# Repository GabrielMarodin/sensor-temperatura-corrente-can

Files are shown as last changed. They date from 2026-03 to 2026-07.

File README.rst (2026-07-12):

Monitoramento de temperatura e corrente via CAN do barco solar
#####################################################################

.. contents::
   :local:
   :depth: 2

Requisitos
**********

Este projeto foi implementado com os seguintes módulos/softwares/hardwares:
 | Sensor de temperatura PT100 com 3 fios.    
 | Sensor de corrente de efeito Hall LEM LA 205-S.  
 | MCP2515 (Controlador CAN);
 | TJA1050 (Transceptor CAN);  
 | Linguagem de programação C.  
 | Microcontrolador STM32F401 com SPI, ADC e regulador de 5V para 3V3.  

Visão geral
***********

Esse projeto faz parta do barco solar Zênite Solar.

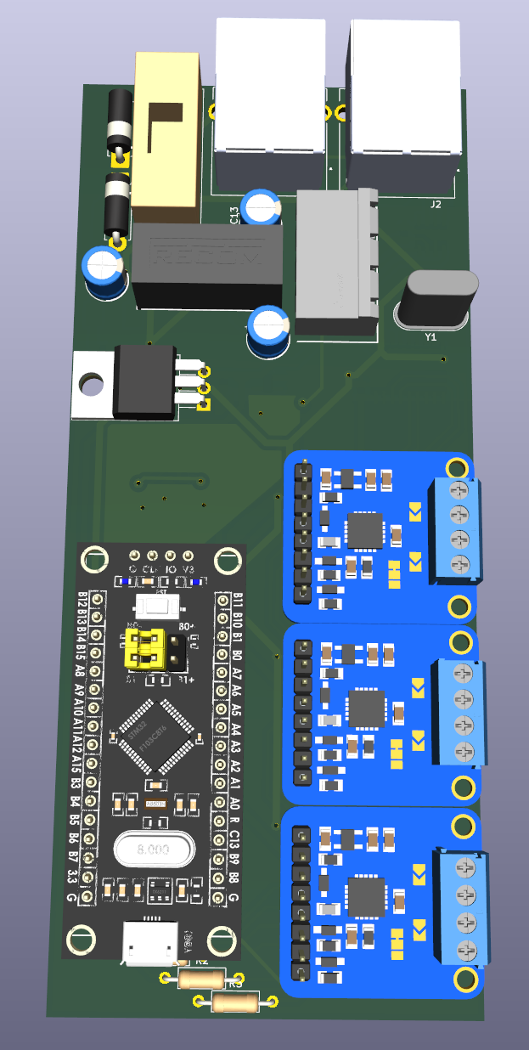
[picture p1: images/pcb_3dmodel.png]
Modelo 3D da placa de circuito impresso


É um sistema microcontrolado embarcado ao barco que possui capacidade de ler temperaturas em pontos estratégicos do barco e a corrente do motor.

O microcontrolador lê e trata os dados e empacota em um frame CAN para transmitir, através a implementação do controlador e transmissor CAN, para a saída do conector RJ45.

O desenvolvimento foi divido em quatro etapas:

- `Etapa 1 </etapa_1>`_ (02/04/2026): Pesquisa, planejamento e outline do projeto.
- `Etapa 2 </etapa_2>`_ (30/04/2026): Teste dos módulos e desenvolvimento de protótipo.
- `Etapa 3 </etapa_3>`_ (28/05/2026): Desenvolvimento do produto.
- `Etapa 4 </etapa_4>`_ (09/07/2026): Implementação e análise de desempenho.

Interface do usuário
********************
LED de respiração:
  Pisca enquanto o RTOS estiver ativo.

Testando
========

Para testar pode ser usado o debugger do microcontrolador para ler as variáveis e registradores ou um analizador de CAN para capturar as mensagens transmitidas.

Montagem
********

O sistema é alimentado e transmite os frames CAN pelo conector RJ45;

O sensor de corretente de efeito hall deve ser conectado no conector de 4 pinos;

O PT100 deve ser conectado no MAX31865 nos conectores de parafuso.

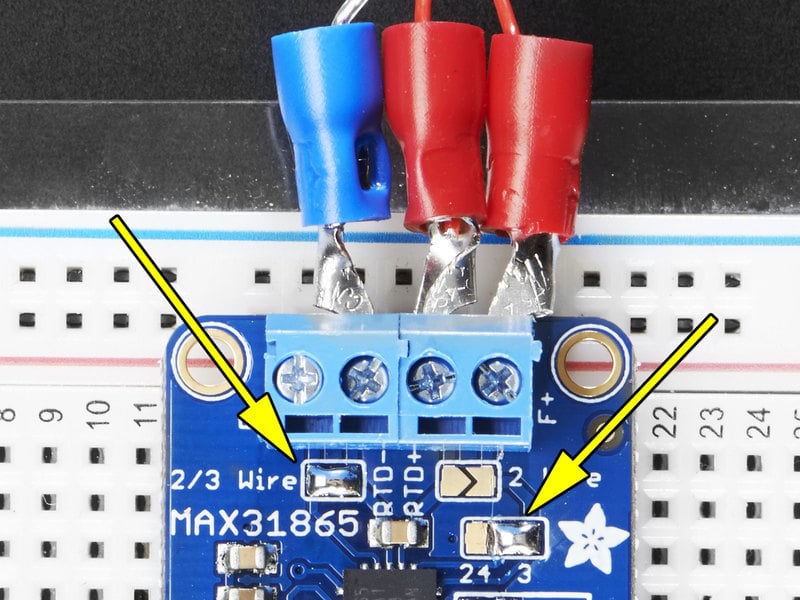
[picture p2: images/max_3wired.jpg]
MAX31865 breakout board com 3 fios conectados


   Modo de conexão de 3 fios do PT100.

   No modo 3 wires 2 fios estão em paralelo e 1 fio tem 100 ohms de resistência a 0 graus celsius em relação aos outros, os fios com resistência muito baixa entre si devem ser conectados em RTD+ e F+, enquanto o terceiro fio deve ser conectado em RTD-.

Referências (Links)
*******************

- `GitHub do Zênite Solar <https://github.com/ZeniteSolar>`_

- `Firmware do Projeto </etapa_4/Firmware>`_

- `Projeto KiCad da PCB </etapa_3/PCB/Modulo_corrente_temperatura_barco_Zenite>`_

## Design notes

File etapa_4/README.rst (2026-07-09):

Etapa 4
#######

.. contents::
   :local:
   :depth: 2

Visão geral
***********

A Etapa 4 abordará projeto do layout e montagem da placa de circuito impresso que abriga o sistema embarcado. A partir da montagem da PCB serão verificados os critérios de desempenho definidos na Etapa 3, juntamente a validação do sistema e integridade dos dados no barco.

Desenvolvimento
***************

Layout da PCB
=============

Para a elaboração do *layout* foram priorizados os seguintes aspectos:

+ Alta densidade de componentes, visando aproveitar o espaço limitado;
+ Segmentação da placa em áreas relacionadas à potência (dissipação de calor e emissão de EMI), tratamento de sinais analógicos e trilhas de sinais digitais;
+ Dedicação de um plano de referência exclusivo para o condicionamento do sinal proveniente do sensor de corrente (visando diminuir erros e aumentar a precisão);
+ Priorização de componentes SMD;
+ As regras de desenho devem ser compatíveis com os limites da CNC do LPAE(IFSC);
+ Placa de face dupla, sendo a camada superior majoritariamente um plano de referência sólido.

Observando as condições de manufatura do IFSC, foram priorizados componentes SMD de tamanho mínimo equivalente ao encapsulamento SOIC para os circuitos integrados e 0805 para capacitores e resistores. O projeto desenvolvido no KiCad pode ser visualizado em: `Link para a versão 1 do projeto <https://github.com/GabrielMarodin/sensor-temperatura-corrente-can/tree/main/etapa_3/PCB/Modulo_corrente_temperatura_barco_Zenite>`_ .

No entanto, alguns componentes estavam indisponíveis e adaptações foram necessárias, como pode ser observado na imagem abaixo.

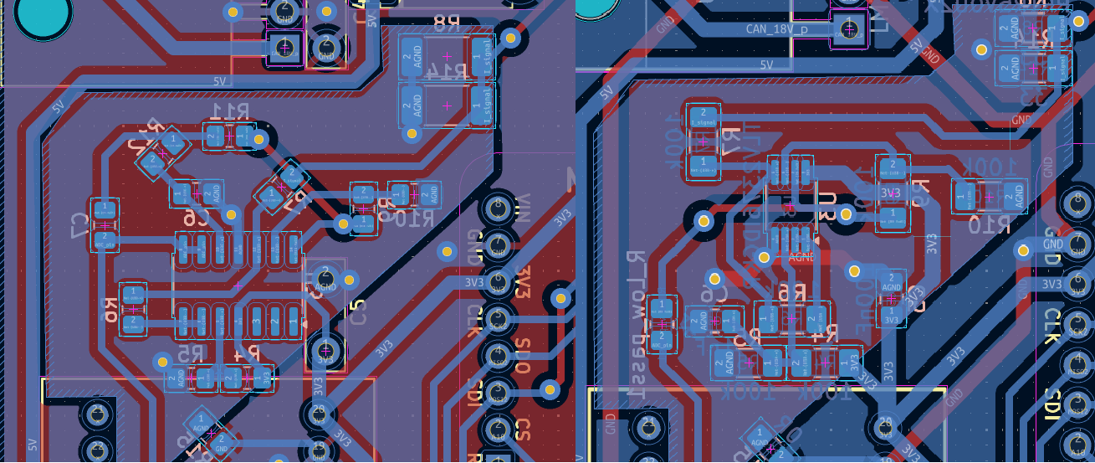
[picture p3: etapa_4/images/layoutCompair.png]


O amplificador operacional TLV9004, inicialmente idealizado, foi substituído pelo TLV2376, em um encapsulamento menor, mas plenamente compatível com os requisitos do projeto. A substituição também ocorreu com o filtro ativo anteriormente previsto que foi trocado por um filtro passivo RC passa-baixa. O *layout* adaptado no KiCad pode ser visualizado em: `Link para a versão 2 do projeto <https://github.com/GabrielMarodin/sensor-temperatura-corrente-can/tree/main/etapa_3/PCB/Modulo_corrente_temperatura_barco_Zenite-V02>`_ .

Montagem da PCB
===============

A fabricação da PCB foi realizada no LPAE com o auxílio de seus técnicos e professores para a operação da CNC. O projeto impresso corresponde à `versão 2 <https://github.com/GabrielMarodin/sensor-temperatura-corrente-can/tree/main/etapa_3/PCB/Modulo_corrente_temperatura_barco_Zenite-V02>`_ . No entanto, algumas modificações foram necessárias, como o corte manual das trilhas e pads do amplificador operacional, além da utilização da técnica de *wire up* para integrar o circuito integrado à placa.

A PCB montada pode ser visualizada nas imagens abaixo:

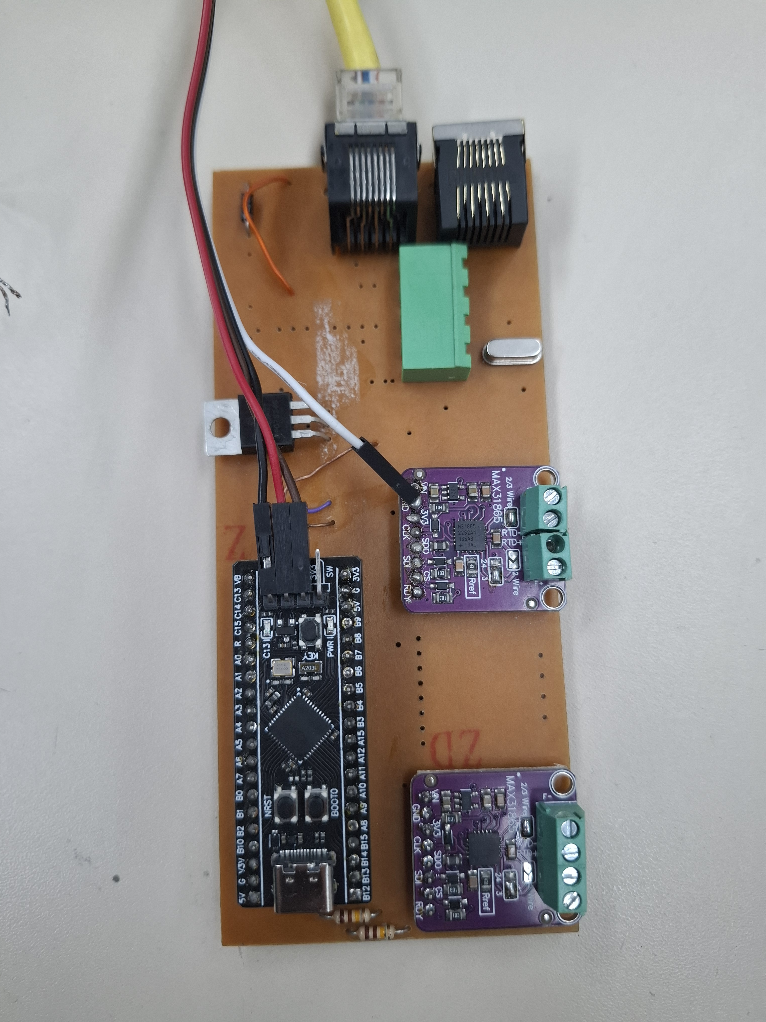
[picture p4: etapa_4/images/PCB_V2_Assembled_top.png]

   
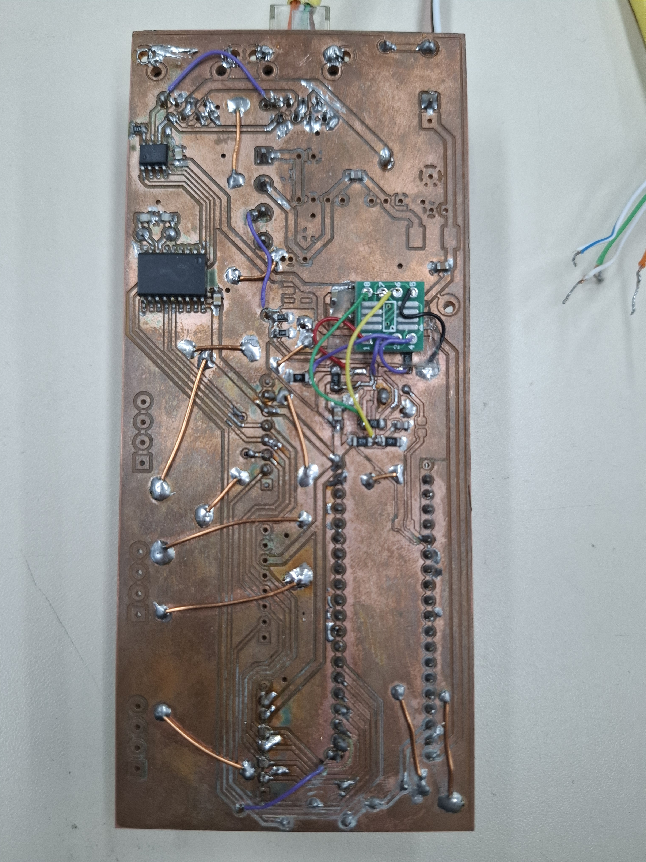
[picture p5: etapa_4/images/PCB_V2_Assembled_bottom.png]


Nota-se nas imagens que há muitos espaços não ocupados por componentes. Esses espaços correspondem a elementos que não estavam disponíveis no momento da montagem, mas que poderão ser inseridos posteriormente, assim que houver disponibilidade. Observa-se também a presença de diversos fios de cobre nu esmaltado na parte inferior da placa. Esses fios foram utilizados para interconectar as ilhas de GND, uma vez que não foi possível fabricar a placa em dupla face e garantir o plano de referência sólido originalmente previsto.

Validação da Aplicação
======================

Validação do Desempenho
***********************

Sensor Hall
======================

O sensor de efeito Hall lido pelo ADC com offset teve os seguintes resultados:

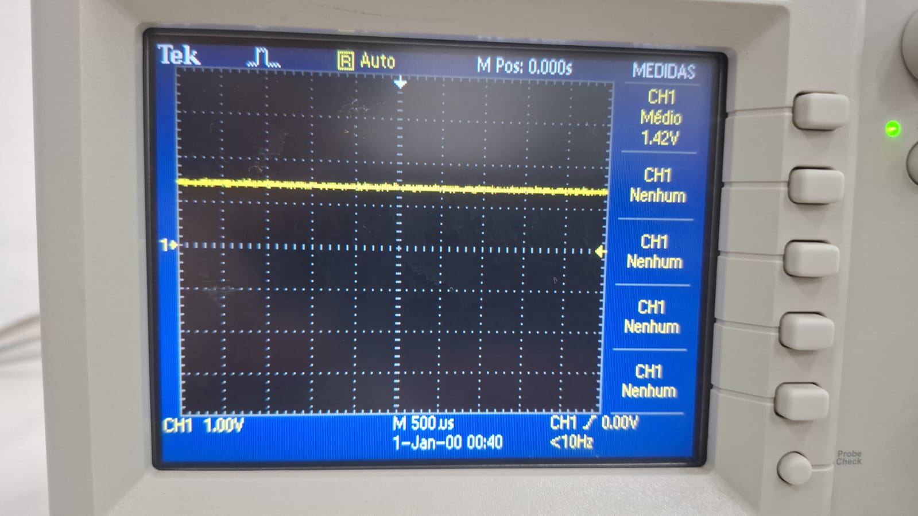
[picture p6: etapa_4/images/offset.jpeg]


A figura mostra o valor real medido do offset no divisor resistivo.

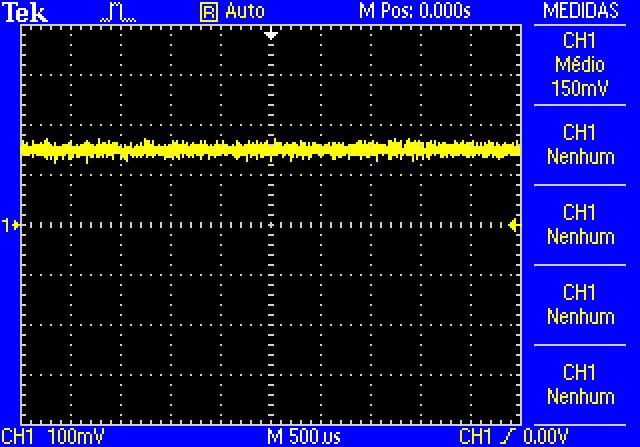
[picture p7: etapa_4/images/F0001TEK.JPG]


A figura mostra o valor de tensão com corrente positiva no shunt de 16 Ohms do sensor de corrente.

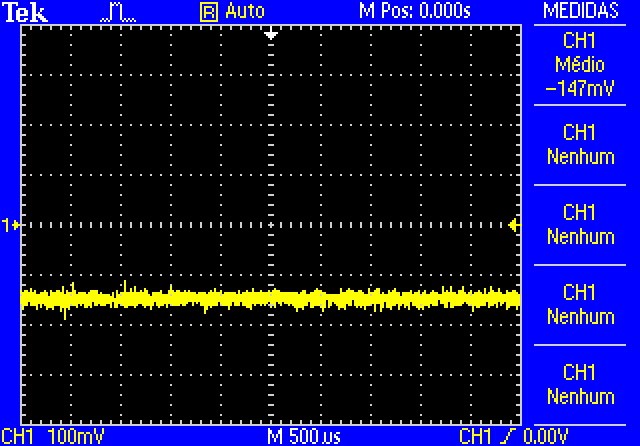
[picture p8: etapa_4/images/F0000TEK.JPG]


A figura mostra o valor de tensão com corrente negativa no shunt de 16 Ohms do sensor de corrente.



A figura mostra o valor lido e convertido utilizando a fórmula `previamente exposta na etapa 2 <../etapa_2/README.rst#L55>`_.

Pode-se concluir que há uma variação de 3 mA o que era esperado para a resolução de 10 bits mais as não idealidades propagadas.

Sensor de temperatura
======================

O sensor temperatura lido pelo SPI da breakout board MAX31865 teve os seguintes resultados:

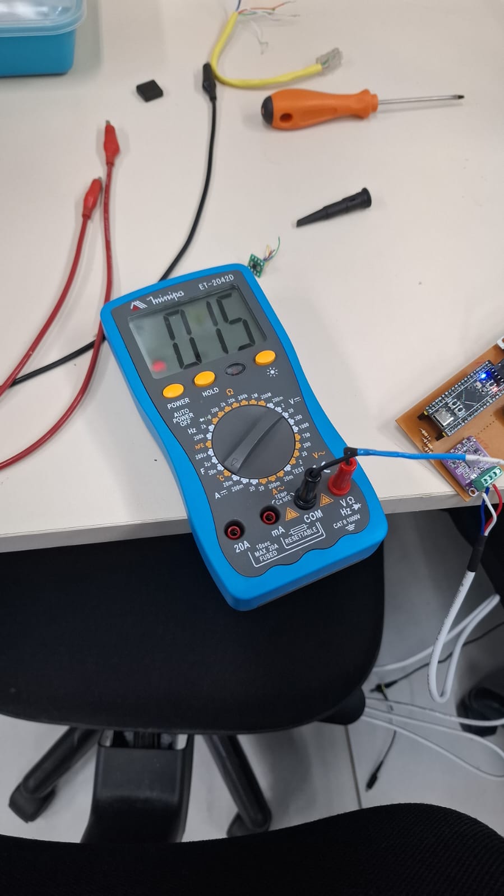
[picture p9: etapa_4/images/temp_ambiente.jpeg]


A figura mostra a temperatura ambiente no momento de teste.

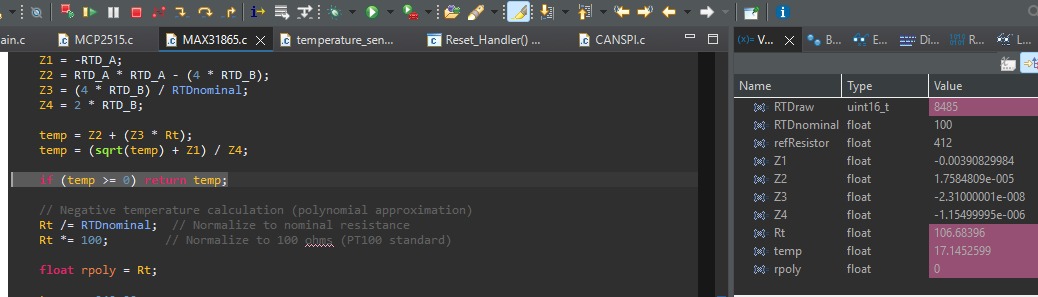
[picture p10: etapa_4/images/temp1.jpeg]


A figura mostra a temperatura lida e calculada do PT100.

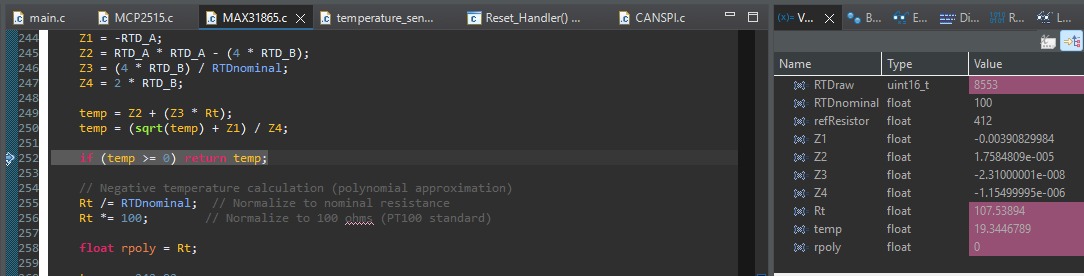
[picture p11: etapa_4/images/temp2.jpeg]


A figura mostra a temperatura do PT100 depois de um tempo em contato com a mão.

O ADC do MAX31865 é de 16 bits com 15 bits de RTD a resolução é alta e o maior fator de erro é o valor do resistor de referência, alterar a macro do software do [RREF] para o valor medido com um multímetro na hora 
afeta a exatidão da temperatura dastricamente.

Estimativas de processamento e desempenho do MCU
======================
Não houve tempo de executar testes quantitativos do processamento da CPU, portanto foram feitas estimativas baseadas
no tempo médio dos processos mais lentos de cada tarefa e gastos típicos de corrente e ocupação da CPU.

O período de ativação das tarefas é muito maior que o tempo de execução da tarefa mais lenta o que permite dizer que o sistema
não tem dificuldade em atender as deadlines e mesmo assim ele é soft real-time considerando que perdas de dados ocasionais não
causarão falhas críticas no sistema em que está embarcado.

Tempo de execução de cada tarefa
--------------------------------

+------------------+-----------------------------------------------+----------------------+
| Tarefa           | Descrição                                     | Tempo estimado       |
+==================+===============================================+======================+
| CurrentTask      | Processamento do buffer ADC                   | 20–60 µs             |
+------------------+-----------------------------------------------+----------------------+
| CANCurrentTask   | Cálculo RMS, pico e envio CAN                 | 180–350 µs           |
+------------------+-----------------------------------------------+----------------------+
| RTDTask          | Leitura de três sensores MAX31865             | 200–225 ms           |
+------------------+-----------------------------------------------+----------------------+
| CANTempTask      | Empacotamento e envio CAN                     | 70–120 µs            |
+------------------+-----------------------------------------------+----------------------+

Tempo de ocupação da CPU
--------------------------------

+---------------------------+----------------+
| Componente                | Utilização     |
+===========================+================+
| Processamento ADC         | 1–3 %          |
+---------------------------+----------------+
| Cálculo da corrente RMS   | 2–5 %          |
+---------------------------+----------------+
| Driver CAN                | < 1 %          |
+---------------------------+----------------+
| Escalonador FreeRTOS      | < 1 %          |
+---------------------------+----------------+
| Processamento RTD         | < 1 %          |
+---------------------------+----------------+
| Total estimado            | 5–10 %         |
+---------------------------+----------------+
| CPU ociosa                | 90–95 %        |
+---------------------------+----------------+

Medição do WCET (Worst-Case Execution Time)
--------------------------------

+------------------+----------------------+------------------------------+
| Tarefa           | WCET estimado        | Observação                   |
+==================+======================+==============================+
| CurrentTask      | 60 µs                | Filtragem e cópia DMA        |
+------------------+----------------------+------------------------------+
| CANCurrentTask   | 350 µs               | Inclui cálculo RMS e CAN     |
+------------------+----------------------+------------------------------+
| RTDTask          | 225 ms               | Inclui atrasos HAL_Delay()   |
+------------------+----------------------+------------------------------+
| CANTempTask      | 120 µs               | Montagem e transmissão CAN   |
+------------------+----------------------+------------------------------+
| RTDTask (CPU)    | 300–500 µs           | Desconsiderando HAL_Delay()  |
+------------------+----------------------+------------------------------+

Eficiência energética da placa
--------------------------------

+--------------------------------+-----------------------------+
| Parâmetro                      | Valor estimado              |
+================================+=============================+
| Frequência do processador      | 84 MHz                      |
+--------------------------------+-----------------------------+
| Consumo típico do STM32F4      | 25–35 mA @ 3,3 V            |
+--------------------------------+-----------------------------+
| Potência estimada do MCU       | 80–115 mW                   |
+--------------------------------+-----------------------------+
| Utilização média da CPU        | 5–10 %                      |
+--------------------------------+-----------------------------+
| Tempo ocioso da CPU            | 90–95 %                     |
+--------------------------------+-----------------------------+
| Uso de DMA                     | Sim                         |
+--------------------------------+-----------------------------+
| Uso de filas do FreeRTOS       | Sim                         |
+--------------------------------+-----------------------------+
| Polling contínuo               | Não                         |
+--------------------------------+-----------------------------+
| Classificação da eficiência    | Alta                        |
+--------------------------------+-----------------------------+

Verificação da Integridade dos Dados
====================================

Referências (links/datasheets/livros)
*************************************

- `Código de interface MCP2515 <https://github.com/eziya/STM32_SPI_MCP2515/tree/master>`_

- `Datasheet do MCP2515 <https://www.microchip.com/en-us/product/mcp2515>`_

- `Datasheet do MAX31865 <https://www.analog.com/media/en/technical-documentation/data-sheets/max31865.pdf>`_

- `Datasheet do TLV2376 <https://www.ti.com/product/TLV2376/part-details/TLV2376IDGKR>`_

- `Datasheet do TJA1050 <https://www.nxp.com/docs/en/data-sheet/TJA1050.pdf>`_

- `Fundamentos da camada física do CAN <https://www.ti.com/lit/an/slla270/slla270.pdf?ts=1783507668427>`_

- `GitHub do Zenite Solar <https://github.com/ZeniteSolar>`_

- `ARM Cortex-M4 Technical Reference Manual (DWT CYCCNT) <https://documentation-service.arm.com/static/5fce431be167456a35b36ade>`_

- `ARM Cortex-M4 Processor Datasheet <https://developer.arm.com/-/media/Arm%20Developer%20Community/PDF/Processor%20Datasheets/Arm%20Cortex-M4%20Processor%20Datasheet.pdf>`_

- `STM32F4 Series Documentation (Reference Manuals and Datasheets) <https://www.st.com/en/microcontrollers-microprocessors/stm32f4-series/documentation.html>`_

- `STM32F407/417 Documentation (Reference Manual RM0090 and Datasheets) <https://www.st.com/en/microcontrollers-microprocessors/stm32f407-417/documentation.html>`_

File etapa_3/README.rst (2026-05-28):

Etapa 3
#######

.. contents::
   :local:
   :depth: 2

Visão geral
***********

A Etapa 3 abordará a implementação do protocolo CAN, bem como a integração e os testes dos dados provenientes dos sensores em um mesmo firmware baseado em arquitetura RTOS. O objetivo é validar o envio correto das informações pelo barramento CAN.

Além disso, será abordado a elaboração do esquemático da placa de circuito impresso, juntamente com a definição dos critérios de desempenho do sistema, que serão avaliados na etapa seguinte.

Desenvolvimento
***************

`Link para os Testes <Testes>`_

Implementação do Protocolo CAN
==============================

O `driver </etapa_3/Testes/pi3_CAN_test/Core/Src/MCP2515_driver.c>`_ do MCP2515 se baseia na implementação da Microchip e utiliza o mapa de registradores do  `datasheet <https://ww1.microchip.com/downloads/en/DeviceDoc/MCP2515-Stand-Alone-CAN-Controller-with-SPI-20001801J.pdf>`_ (tabelas 11-1 e 11-2).
O MCP2515 é configurado para ter sua divisão de clock de 8 MHz de forma a transmitir em 500 Kbps;

Integração dos dados dos sensores à aplicação
=============================================

Os dados dos sensores foram arranjados da seguinte maneira:

Temperatura:

+-------------------+----------------+
|        Dado       | Tamanho (Bits) |
+===================+================+
|    Temp. Motor    |       10       |
+-------------------+----------------+
| Temp. Controlador |       9        |
+-------------------+----------------+
|   Temp. Bateria   |       10       |
+-------------------+----------------+
|  Falha Detectada  |        3       |
+-------------------+----------------+

Foi alterado para possibilitar o relatório de erro individual de cada sensor.

Corrente:

+---------------------+----------------+
| Dado                | Tamanho (Bits) |
+=====================+================+
| Corrente de Pico    | 12             |
+---------------------+----------------+
| Sentido do Pico     | 1              |
+---------------------+----------------+
| Corrente RMS        | 12             |
+---------------------+----------------+
| Sentido da Corrente | 1              |
+---------------------+----------------+
| Mensagem de Erro    | 7              |
+---------------------+----------------+

Estes dados foram integrados em pacotes com o seguinte código:

`sensor de corrente </etapa_3/Firmware/Core/Inc/current_sensor.h>`_:

.. code-block:: C

	typedef struct __attribute__((packed)) {
      uint32_t Peak_Current : 11; // Corrente de Pico
      uint32_t Peak_Dir     : 1;  // Sentido da Corrente de Pico
      uint32_t Current_RMS  : 12; // Corrente RMS
      uint32_t Current_Dir  : 1;  // Direção Principal da Corrente
      uint32_t Error_msg    : 7;  // Mensagens de Erro
   } Current_pkg;

`sensores de temperatura </etapa_3/Firmware/Core/Inc/temperature_sensor.h>`_:

.. code-block:: C

   typedef struct __attribute__((packed)) {
      uint32_t Motor_Temp  : 10; // Temperatura do Motor
      uint32_t Charge_Temp : 9;  // Temperatura dos Controladores de Carga
      uint32_t Batt_Temp   : 10; // Temperatura da Bateria
      uint32_t Error_msg   : 3;  // Mensagens de Erro
   } Temp_pkg;

- `Link para o firmware </etapa_3/Firmware>`_

Teste da Rede CAN com Dados dos Sensores
========================================
Após implementação em código do `sensor de corrente </etapa_3/Testes/Sensor_RTOS/Core/Src/Current_Sensor.c>`_ 
e dos `sensores de temperatura </etapa_3/Testes/Sensor_RTOS/Core/Src/Temperature_Sensor.c>`_, foi implementada 
à partir do `driver do MCP2515 </etapa_3/Testes/Sensor_RTOS/Core/Src/MCP2515_Driver.c>`_ a transmição dos 
dados dos sensores utilizando o protocolo CAN nos IDS 0x10 e 0x11. O teste foi realizado utilizando um 
`ESP 32 </etapa_3/Testes/ESP32devkit/ESP32MCP2515>`_ como nó receptor, com o blackpill STM atuando como 
nó transmissor enviando mensagens.

Segue uma imagem do teste da rede CAN, o osciloscópio mede a tensão diferencial da linha no módulo utilizado.

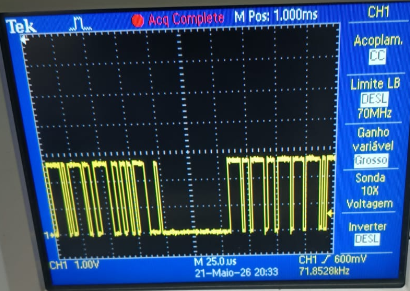
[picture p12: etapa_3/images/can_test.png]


O ESP32 foi configurado para repassar as mensagems que recebe por SPI do MCP2515 para a porta 
serial, e o terminal do computador foi configurado para receber as mensagens. Devido à um problema de comunicação,
não foi possível realizar a leitura da rede CAN.

Esquemático da PCI
==================

O projeto KiCad onde foi elaborado o esquemático pode ser encontrado em:  `Link para o Esquemático do Projeto <https://github.com/GabrielMarodin/sensor-temperatura-corrente-can/tree/main/etapa_3/PCB/Modulo_corrente_temperatura_barco_Zenite>`_ 

O esquemático apresentado em partes nos próximos tópicos foi desenvolvido para atender aos requisitos do projeto, considerando:

- Níveis de tensão e corrente necessários para cada sensor e circuito integrado.

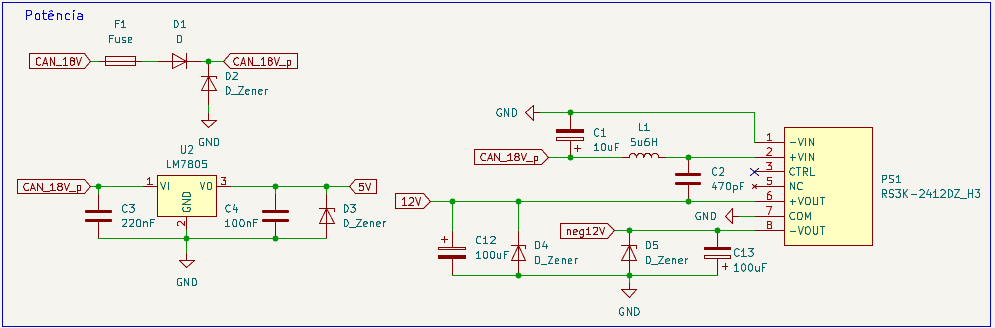
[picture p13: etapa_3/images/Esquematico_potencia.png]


Na figura acima é possível observar elementos de proteção contra sobrecorrente e surtos de tensão, além de um regulador linear destinado à alimentação do microcontrolador e de um conversor estático responsável por suprir as necessidades do sensor de corrente utilizado.

- Conexão com a rede CAN, alimentação do módulo e do sensor de corrente.

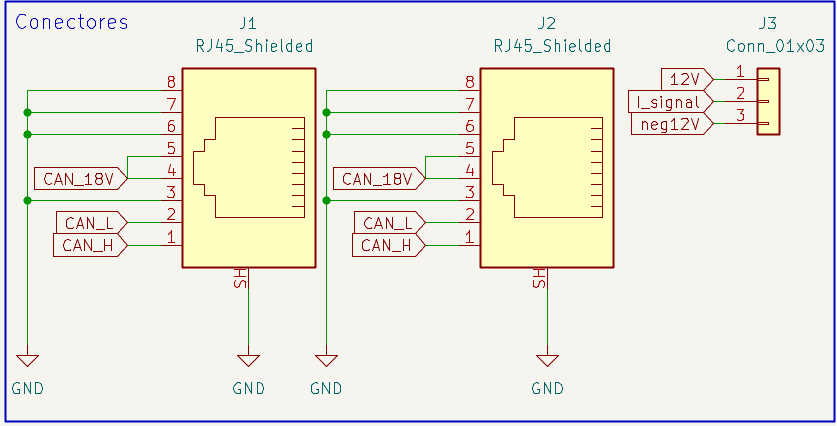
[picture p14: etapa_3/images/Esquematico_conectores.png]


Além dos conectores RJ45 padrão do barco foi necessário a previsão de um conector 3 pinos genérico para a alimentação e retorno do sinal em corrente do LA 205-s.

- Condicionamento do sinal de corrente do LA 205-s.

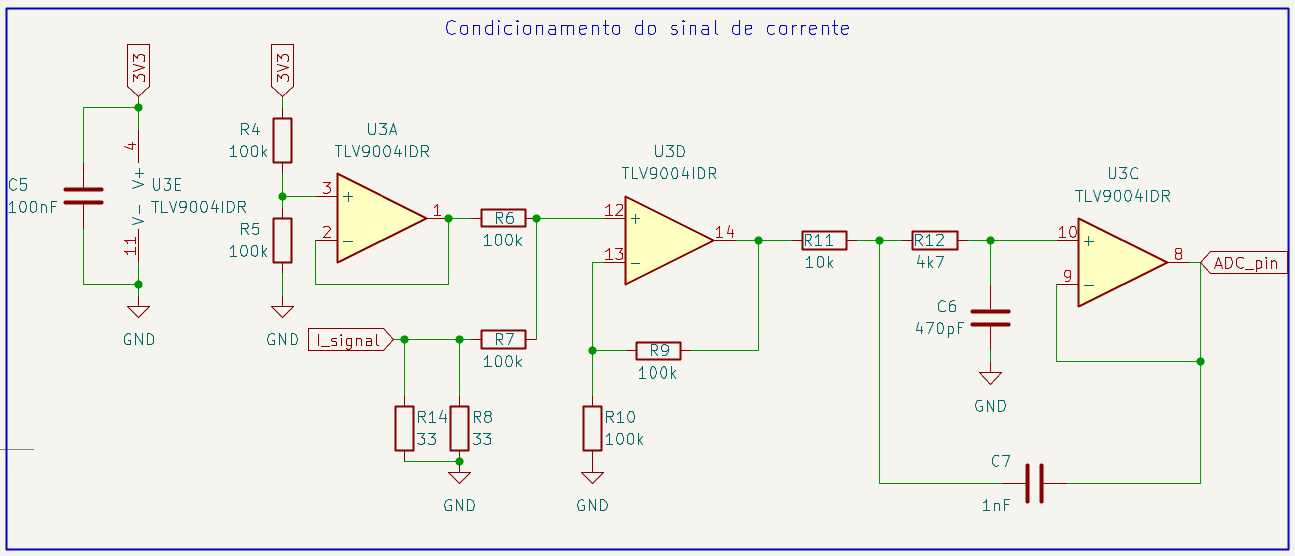
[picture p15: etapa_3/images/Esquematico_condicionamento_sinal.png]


Observa-se na figura a presença de amplificadores operacionais configurados em diferentes topologias: buffer (para sinal de referência), somador não inversor (para obtenção do offset) e filtro ativo passa-baixa de segunda ordem.

   O circuito funciona de modo que:

   - 1,65 V na saída representam 0 A;
   - 3,3 V na saída correspondem a +200 A;
   - 0 V na saída equivalem a –200 A.
 
Ressalta-se que, atualmente, a frequência de corte do filtro encontra-se próxima de 120 kHz. No entanto, essa configuração pode ser ajustada posteriormente, mediante análise da forma de onda real da corrente do motor.

- Gerenciamento e envio de mensagens CAN.

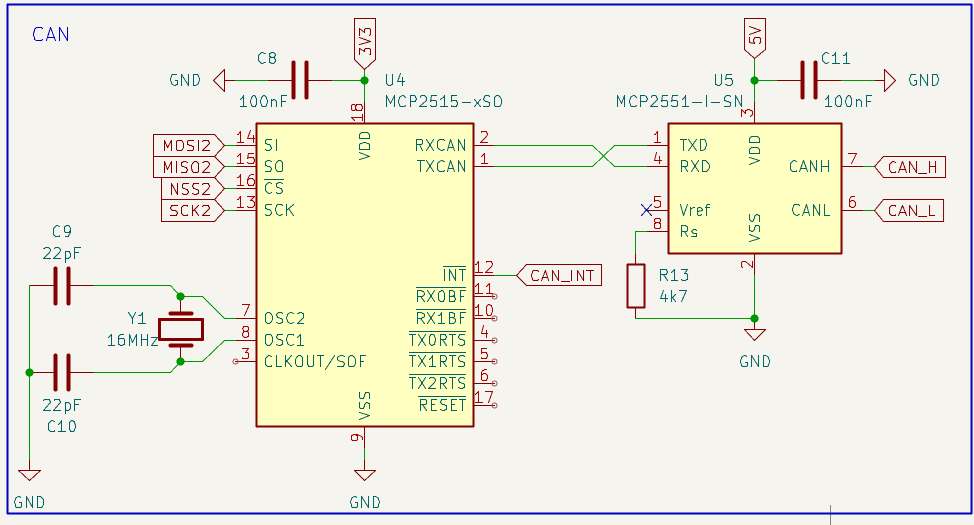
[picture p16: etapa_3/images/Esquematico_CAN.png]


Na figura acima obeserva-se os CIs responsáveis pelo gerenciamento do protocolo e transdução do sinal.

- Processamento de dados e transdução da temperatura.

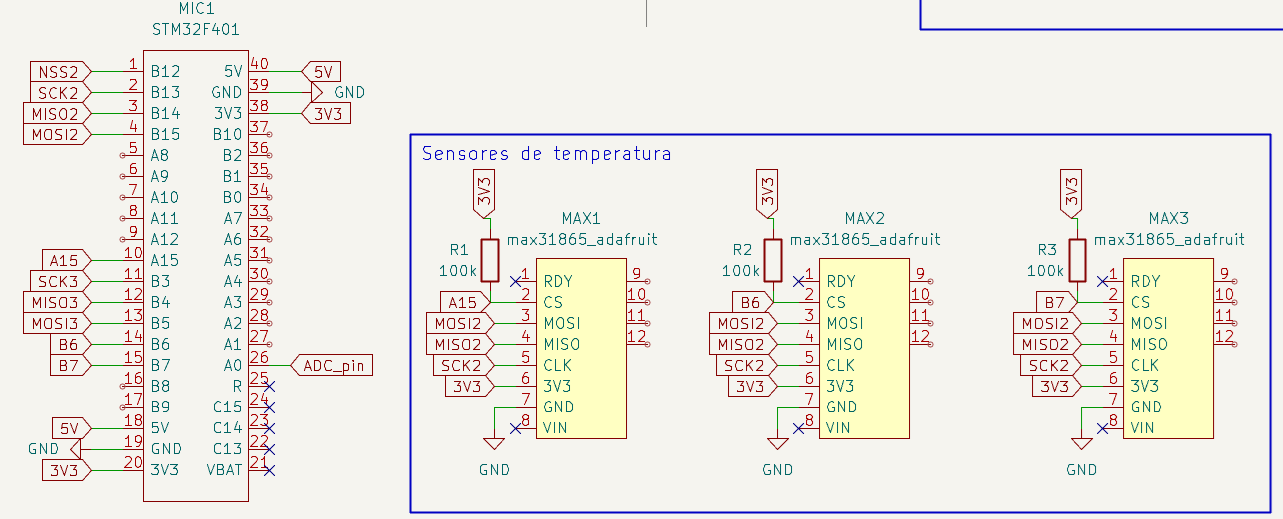
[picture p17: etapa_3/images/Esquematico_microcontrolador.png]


Na figura acima observa-se a atribuição dos pinos no microcontrolador, além dos três módulos baseados no circuito integrado MAX31865. Ressalta-se que existe a possibilidade de substituir os módulos pelo próprio CI, entretanto, devem ser consideradas as restrições de fabricação da placa em virtude do encapsulamento do MAX31865.

Critérios de Desempenho
***********************

Os critérios de desempenho adotados para o projeto, que deverão ser medidos na próxima etapa, são:

- Tempo de execução de cada tarefa;
- Tempo de ocupação da CPU;
- Medição do WCET (Worst-Case Execution Time);
- Eficiência energética da placa;
- Exatidão das medidas de corrente e temperatura, para fins de validação do código.

Referências (links/datasheets/livros)
*************************************

- `Código de interface MCP2515 <https://github.com/eziya/STM32_SPI_MCP2515/tree/master>`_

- `Datasheet do MCP2515 <https://www.microchip.com/en-us/product/mcp2515>`_

- `GitHub do Zenite Solar <https://github.com/ZeniteSolar>`_

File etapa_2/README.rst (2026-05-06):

Etapa 2
#######

.. contents::
   :local:
   :depth: 2

Visão geral
***********

A etapa 2 abordará os testes dos sensores de temperatura e corrente em placas de desenvolvimento e a definição da arquitetura do protoloco CAN que será implementado no sistema embarcado referente ao projeto em questão.

Desenvolvimento
***************

Testes
======

**Aquisição de Temperatura com o MAX 31865**

Foi conectado o sensor MAX 31865 por SPI ao blackpill e requisitada sua leitura. Testado com temperatura ambiente de 22°C e temperadura levemente elevada por fricção

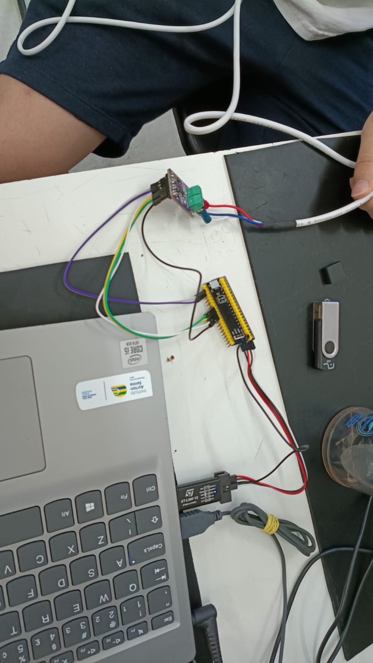
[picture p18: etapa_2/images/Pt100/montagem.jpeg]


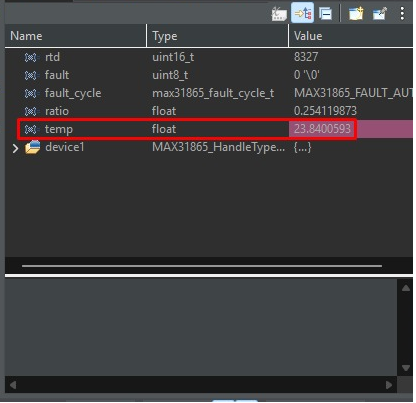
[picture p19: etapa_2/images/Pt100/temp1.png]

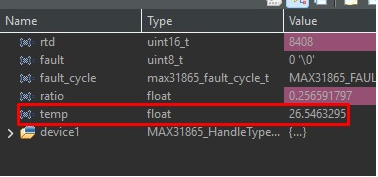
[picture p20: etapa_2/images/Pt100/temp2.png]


**Medição de Corrente com LA 205-S**

Para os testes com o sensor LEM LA205S com correntes positivas e negativas, foi utilizada a seguinte topologia:

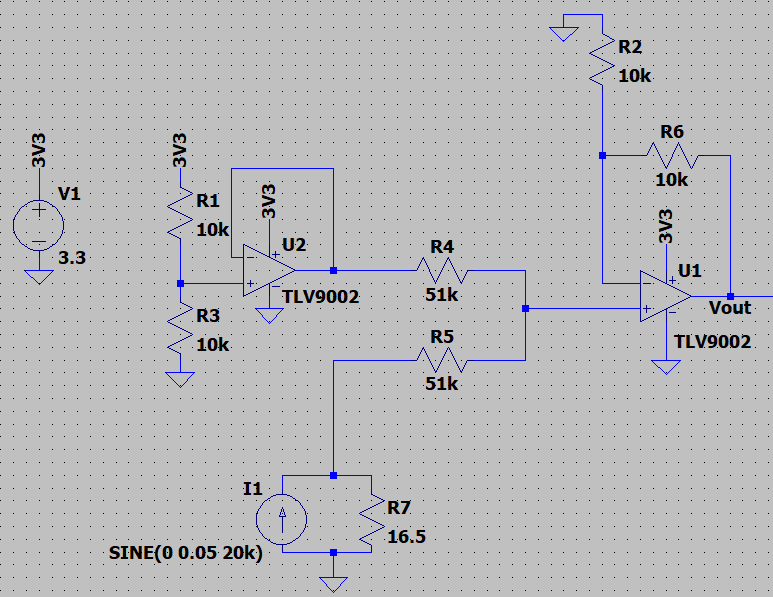
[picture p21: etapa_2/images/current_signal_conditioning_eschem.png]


Temos que a saída do circuito é igual a $V_{ADC}=V_{Shunt}+V_{off}=I_{Shunt}R_{Shunt}+V_{off}$, isolando para a corrente $I_{Shunt}$, temos que $I_{Shunt}=(V_{ADC}-V_{off})/R_{Shunt}$

Foi configurado o ADC do blackpill para uma frequência de amostragem de 120 kHz com 10 bits de precisão, foi então utilizada uma fonte linear para emular a tensão do shunt

Foi então calculada a corrente esperada no pino com offset ($I_{real}=(V_{ADC}-V_{offset})/R_{shunta}$), como $V_{offset}=V_{dd}/2$ e $R_{shunt}=16$, sendo calculada pela seguinte fórmula dentro do callback do ADC:

.. code-block:: C

	uint32_t milli_volt = (ADC_reading*3300)>>10;
	Current_Measured = (milli_volt-(3300>>1))>>4;

Sendo `Current_Measured` a corrente do secundário em $mA$

Valor de corrente medido:

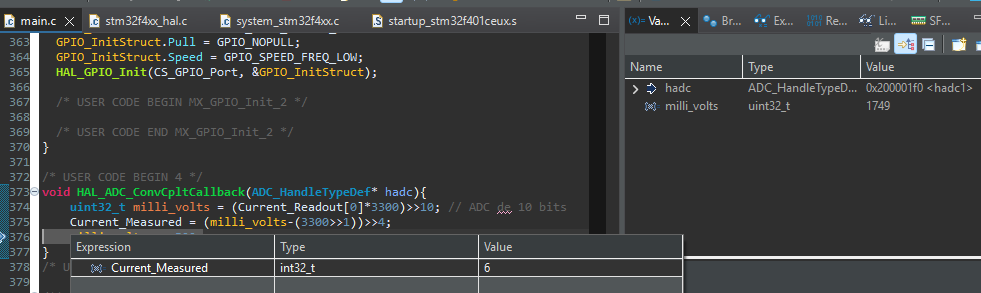
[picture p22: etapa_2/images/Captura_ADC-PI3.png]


O valor da variável milli_volt está coerente com o esperado do valor da fonte, sendo que $6mA$ no resistor de shunt resultaria em uma tensão de $6 * 16=96mV$ - após amplificação, o pino do ADC mede $96+3300/2=1746mV$, conforme esperado

Testando o circuito amplificador com uma fonte linear, obtemos leituras no ADC de $1981mV (21mA)$ e $673mV(-61mA)$ respectivamente.

Para calcular a corrente do primário, precisamos multiplicar o resultado final por 2000, como há uma divisão por 16 no final do código, podemos apenas remover $>>4$ e o substituir por $*125$, resultando no seguinte código:

.. code-block:: C

	uint32_t milli_volt = (ADC_reading*3300)>>10;
	Current_Measured = (milli_volt-(3300>>1))*125;

Podemos estimar a resolução da leitura final no lado do primário da seguinte maneira:

$ADC=3300/10^{10}=3,22 mV$

$I_{Sec}=ADC/R_{Shunt}=0,2014 mA$

$I_{Pri}=I_{Sec}*2000=402,83 mA$

Como $400/10^{10}=390mA$, temos uma pequena perda na resolução final em relação aos 10 bits utilizados do ADC, mas ainda dentro dos requisitos iniciais do projeto ($>1A$)

Arquitetura do Protocolo CAN
============================

O microcontolador STM32f401 (blackpill) não possui o periférico CAN nativo, logo, se faz necessário uma interface controladora que torna possível a implementação do protocolo sem gerar custos adicionais a CPU do microcontrolador.
A interface do microcontrolador com a rede CAN será feita por intermédio de dois circuitos integrados:

+ MCP2515 -> Controlador CAN
+ TJA1050 -> Transceptor CAN

A implemetação física pode ser observada pelo diagrama a seguir:


   
O protocolo CAN a ser impletamentado pertence a versão 2.0A, conhecido também como "standard CAN".
Seu dataframe pode ser observado na imagem abaixo:

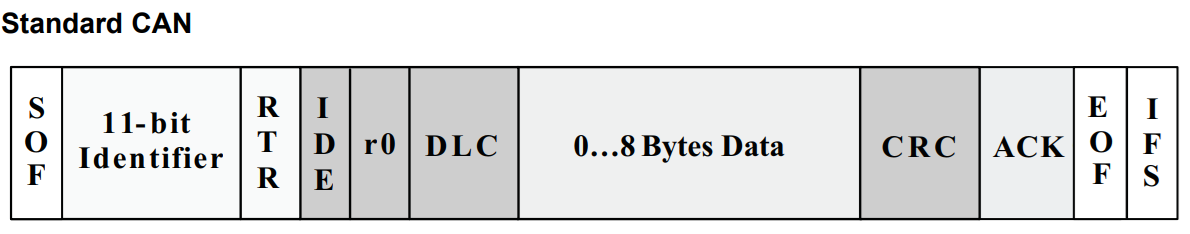
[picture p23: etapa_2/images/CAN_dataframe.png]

   
Para o projeto em questão é necessário que o microcontrolador somente envie mensagens.

Para implementar a arquitura utilizando o controlador CAN MCP2515 é necessário, através do barramento SPI:

+ Configurar o *baud rate* (registradores CNF[1:3])
+ Habilitar feedback de envio (registrador CANINTE) -> permite debug
+ Escolher modo de operação (Normal, sleep, loopback...) (registrador CANCTRL)

+ Configurar o *identifier* de 11 bits (registradores TXBnSIDH e TXBnSIDL)
+ Escolher o tamanho do pacote de dados (0 a 8 bytes) (registrador TXBnDLC)
+ Carregar dados (registradores TXBnD[0:7])
+ Escolher o buffer que será transmitido (registrador TXRTSCTRL)
+ Requisitar envio do buffer (registrador TXBnCTRL)

Os demais campos do dataframe do protocolo tais como CRC, ACK e EOF serão calculados e gerados pelo controlador CAN.

O nó da rede CAN em questão possuirá 2 *identifiers*:

+ Id zzz contendo as aquisições de temperatura.
+ Id xxx contendo as medições de corrente.

As mensagens serão divididas da seguinte forma:

	**Id zzz**

+ Frequência de envio = 1 - 5 Hz;
+ Total bytes = 4;
+ bits[31:30] -> informa status da aquisição ou erro nos sensores (00b = sem falhas; 01b = falha no sensor do motor; 10b = falha no sensor dos controladores; 11b = falha no sensor das baterias);
+ bits[29:20] -> Temperatura das baterias em °C;
+ bits[19:10] -> Temperatura dos controladores de carga em °C;
+ bits[9:0]   -> Temperatura do motor em °C.

Para os valores de temperatura deve-se considerar uma casa decimal implicita, por exemplo:

uint16_t t_batt = 822;

corresponde a 82,2°C
	
	**Id xxx**

+ Frequência de envio = 100 - 130 Hz;
+ Total bytes = 4;
+ bits[31:25] -> informa status da aquisição ou erro nos sensores (0000000b = sem falhas; 0000001b = falha de aquisição de corrente de pico; 0000010b = falha de aquisição de corrente RMS);
+ bit[24]     -> informa sentido predominante da corrente (1 para positivo);
+ bits[23:12] -> Corrente RMS em $mA$;
+ bit[11]     -> Sentido da corrente de pico (1 para positivo);
+ bits[10:00] -> Corrente de pico em $mA$.

Para o valores de corrente deve-se considerar o valor multiplicado por 100 em $mA$, por exemplo:

uint16_t rms_I = 1234;

corresponde a 123.400 mA.

Referências (links/datasheets/livros)
*************************************

- `MCP2515 documentação <https://www.microchip.com/en-us/product/mcp2515>`_

- `Zênite Solar GitHub <https://github.com/ZeniteSolar>`_

- `LA 205-S documentação <https://www.lem.com/sites/default/files/products_datasheets/la_205-s.pdf>`_

- `MAX31865 documentação <https://www.analog.com/media/en/technical-documentation/data-sheets/max31865.pdf>`_

- `MAX31865 código fonte base para STM32 <https://github.com/marwen-maghrebi/Advanced-STM32-Simulations-/tree/main/27-STM32_Thermocouple_MAX31865>`_

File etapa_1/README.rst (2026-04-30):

Etapa 1
#######

.. contents::
   :local:
   :depth: 2

Visão geral
***********

A primeira etapa abordará os requisitos e as tecnologias do sistema embarcado que comporá o barco Guarapuvu II, da equipe de competição Zênite Solar do IFSC, a ser desenvolvido durante a unidade curricular Projeto Integrador III do curso de Engenharia Eletrônica.

Além da definição dos requisitos e da tecnologia a ser empregada, serão apresentados:

+ Desenho representativo do barco com os aspectos relevante para o projeto;
+ Fluxograma do funcionamento do sistema;
+ Limitações físicas da PCB a ser desenvolvida;
+ Inventário de componentes necessários para a execução das próximas etapas.

Desenvolvimento
***************

Levantamento de Requisitos
==========================

**Escopo do Sistema**

O sistema contempla:

+ Monitoramento de temperatura em três divisões críticas do barco (Banco de baterias, controladores de carga e Motor);
+ Medição de corrente elétrica na entrada do motor;
+ Condicionamento e conversão dos sinais analógicos para digital;
+ Comunicação dos dados via rede CAN.

**Requisitos Funcionais**

+ Deve ser possível realizar a aquisição de temperatura de até 70°C em três pontos distintos;
+ Deve ser possível realizar a medição de corrente até 200 A;
+ O sistema deve realizar a leitura contínua dos sensores de temperatura e corrente;
+ O sistema deve aplicar condicionamento de sinal adequado para leitura do sensores;

   **Conversão de Sinais**

+ O sinal analógico deve ser convertido com a precisão, resolução e frequência suficientes para seu aproveitamento.

   **Processamento de Dados**

+ O sistema deve processar os dados adquiridos, aplicando por exemplo: Filtragem de ruído, conversão para unidades físicas (°C e A);
+ O sistema deve validar os dados adquiridos, identificando possíveis falhas de sensores.

**Requisitos não Funcionais**

+ O sistema deve atualizar as medições com uma frequência mínima de 20 Hz para as temperaturas e 24 kHz para a corrente;
+ A latência entre aquisição e transmissão não deve exceder 50 ms.
+ O sistema deve operar de forma contínua durante toda a operação do barco.
+ O sistema deve ser robusto a interferências eletromagnéticas (EMI/EMC), típicas de ambientes com conversores e motores elétricos.
+ O sistema deve detectar falhas nos sensores e comunicar estados de erro via CAN.
+ O sistema deve possuir proteção contra surtos e ruídos elétricos.
+ A medição de temperatura deve ter precisão mínima de 0,5 °C.
+ A medição de corrente deve ter erro o menor erro possível.
+ As mensagens devem seguir um formato padronizado e documentado.
+ O sistema deve ter baixo consumo energético para não afetar a autonomia do barco.
+ O sistema deve suportar: Umidade elevada, vibração mecânica, temperaturas variáveis, corrosão.
+ O sistema deve permitir fácil substituição dos sensores.
+ O firmware deve permitir atualização para melhorias futuras.

**Restrições Funcionais**

+ Deve-se usar o sensor de temperatura **PT100** com 3 fios.
+ Deve-se usar o sensor de corrente de efeito *Hall* **LEM LA 205-S**.
+ A versão do protocolo CAN deve ser a versão atual do barco (2.0B).
+ O firmware deve ser escrito na linguagem de programação C.
+ O microcontrolador usado deve ser o STM32F401.

Tecnologias do Projeto
======================

**Aquisição de Temperatura**

Para as aquisições de temperatura serão utilizados o sensor **PT100**, em conjunto com um módulo contendo o conversor analógico-digital **MAX31865**, específico para essa aplicação. Esse módulo dispensa a necessidade de pré-amplificação e filtragem do sinal, simplificando o processo de medição. A frequência de atualização mínima de cada sensor será de 20 Hz.

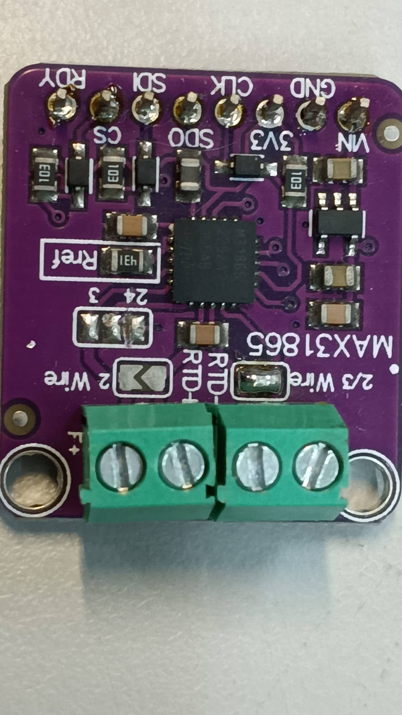
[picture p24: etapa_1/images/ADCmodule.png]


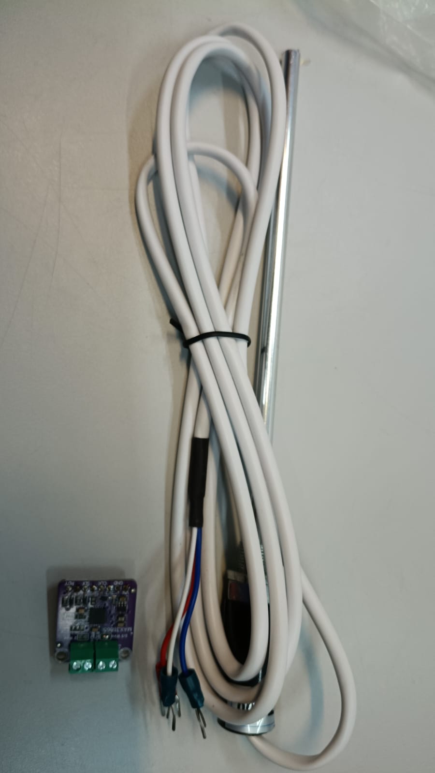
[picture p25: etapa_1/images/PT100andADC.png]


**Medição de Corrente**

Para a medição de corrente será utilizado o sensor de efeito *Hall* **LA 205-S** da **LEM**. A saída de corrente fornecida pelo sensor deve ser transduzida para um nível de tensão adequado, garantindo tanto a precisão da medida quanto a compatibilidade com o ADC empregado.
Além disso, será necessário implementar um filtro passa baixa compatível com a frequência de operação máxima de 12 kHz do motor, assegurando a integridade do sinal adquirido. A fim de respeitar o critério de *Nyquist*, a frequência de amostragem deve ser maior que 24 kHz.

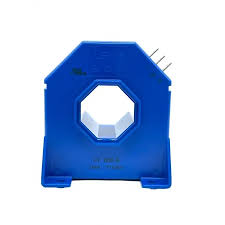
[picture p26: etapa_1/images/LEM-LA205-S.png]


**Conversão de Sinais**

O sistema deve converter todos os sinais analógicos para formato digital, utilizando os conversores A/D do microcontrolador **STM32F401** para a medição de corrente e o **MAX31865** para a aquisição de temperatura. A resolução da conversão deve ser suficiente para garantir a precisão adequada das medições. Na configuração atual do módulo, obtém-se uma resolução de 0.03125 °C para a temperatura e, para a corrente, considera-se que a corrente máxima de 200 A corresponde ao limite da escala de 12 bits e, portanto, a resolução é de 48,828 mA.



**Comunicação CAN**

O sistema deve transmitir os dados referentes as grandezas medidas via rede CAN na versão atual do barco (2.0A). A frequência de transmissão será limitada pela disponibilidade da rede CAN. Quando as medidas forem solicidadas, as últimas medidas imediatas de corrente (pico e média) e temperatura serão enviadas, atentando-se ao limite de 8 bytes do campo de dados.

Desenho Representativo do Barco
===============================


Fluxograma do Funcionamento do Sistema
======================================


Limitações Físicas da PCB
=================================

A placa de circuito impresso a ser desenvolvida deve se enquadrar no suporte reservado a placas do mesmo tipo. Suas dimensões máximas devem ser de 15 cm de comprimento por 6 cm de largura.



Inventário de Componentes necessários
=====================================

Considerando que a etapa 1 aborda uma visão macroscópica do projeto, é possível que haja a adição posterior de componentes para a sua finalização, principalmente no que se refere aos elementos a serem inseridos na PCB. A seguir, são apresentados os componentes previstos para utilização, pelo menos até a terceira etapa do desenvolvimento.

+ 3 unidades do módulo conversor **MAX31865**;
+ 3 unidades do sensor **PT100**;
+ 1 unidade do sensor de efeito *Hall* **LEM LA 205-S**;
+ Resistores variados;
+ Capacitores variados;
+ Diodo para retificação do sinal de corrente;
+ 1 Amplificador operacional *rail-to-rail*;
+ 1 kit de desenvolvimento baseado no microcontrolador STM32F401;
+ 1 regulador linear (Vin >= 18 V, Vout = 3V3);
+ 2 unidades de modulo de comunicação CAN.

Referências (links/datasheets/livros)
*************************************

- `Zênite Solar GitHub <https://github.com/ZeniteSolar>`_

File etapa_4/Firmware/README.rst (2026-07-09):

Firmware
#######

.. contents::
   :local:
   :depth: 2

Visão geral
***********

O código do STM32F401 utiliza FreeRTOS para gerenciar a utilização do MCU pelas tarefas.

Desenvolvimento
***************

Tarefas
=======
`RTDTask <Core/Src/temperature_sensor.c#L48>`_ :
   Utiliza o driver do MAX31865 para pegar as temperatura já convertidas pelo driver e os erros se existirem. Ela salva em uma fila que será consumida pela tarefa do CAN.

`CANTempTask <Core/Src/temperature_sensor.c#L74>`_ :
   Consome os dados da fila e monta o pacote no formato CAN com as temps. e os erros e envia o pacote via SPI.

`CurrentTask <Core/Src/current_sensor.c#L78>`_ :
   Ativa por interrupção, ela filtra os valores do buffer do ADC via um butterworth IIR e salva na fila os dados filtrados para o CAN.

`CANCurrentTask <Core/Src/current_sensor.c#L103>`_ :
   Consome os dados da fila e monta o pacote no formato CAN com o valor RMS e pico e o sentido da corrente e envia o pacote via SPI.

Sequência de funcionamento das tarefas
======
Corrente::

   DMA callback (Half)
      ↓
   CurrentTask
      ↓
   IIRFilter (Half)
      ↓
   DMA callback (Full)
      ↓
   CurrentTask
      ↓
   IIRFilter (Full)
      ↓
   CANCurrentTask wakes up
      ↓
   Calculate RMS and peak
      ↓
   send via CAN

Temperatura::

   TIM3 ISR trigger
      ↓
   RTDTask
      ↓
   Temperatures and faults updated
      ↓
   CANTempTask wakes up
      ↓
   send via CAN

Pinout do Blackpill
======

============ ==========  
Blackpill    Devices 
============ ==========
PA8 	       MAX31865 CS Device 1
PA9 	       MAX31865 CS Device 2
PA10 	       MAX31865 CS Device 3
PB13 	       MAX31865 SCLK
PB14	       MAX31865 MISO
PB15	       MAX31865 MOSI
PB12	       MCP2515 CS
PB13 	       MCP2515 SCLK
PB14	       MCP2515 MISO
PB15	       MCP2515 MOSI
PA0	       ADC Input
============ ==========

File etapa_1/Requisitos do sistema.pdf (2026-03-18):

INSTITUTO FEDERAL DE EDUCAÇÃO, CIÊNCIA E TECNOLOGIA DE SANTA CATARINA - CAMPUS FLORIANÓPOLIS Departamento Acadêmico de Eletrônica Curso de Engenharia Eletrônica

Documento de Requisitos – Sistema de Monitoramento Embarcado

### 1. Visão Geral

Este documento descreve os requisitos de um sistema embarcado de monitoramento para um barco movido a painéis solares. O sistema é responsável pela aquisição de dados de temperatura em áreas críticas e da corrente elétrica do motor, realizando o condicionamento, digitalização e transmissão dos dados via rede CAN para o sistema central de controle.

### 2. Escopo do Sistema

O sistema contempla:

Monitoramento de temperatura em três áreas distintas;

Medição de corrente elétrica na entrada do motor;

Processamento e conversão dos sinais analógicos para digital;

Comunicação dos dados via rede CAN.

### 3. Requisitos Funcionais

3.1 Aquisição de Temperatura

RF01: O sistema deve medir a temperatura em três pontos distintos utilizando sensores do tipo PT100.

RF02: Cada sensor deve estar fisicamente instalado nas áreas de interesse.

RF03: O sistema deve realizar a leitura contínua dos sensores de temperatura.

RF04: O sistema deve aplicar condicionamento de sinal adequado para leitura dos sensores PT100 (ex: ponte de Wheatstone, amplificação, linearização).

3.2 Medição de Corrente

RF05: O sistema deve medir a corrente elétrica na entrada do motor utilizando um sensor do tipo amperímetro de efeito Hall.

RF06: A medição deve ser não invasiva (sem necessidade de interrupção do condutor).

RF07: O sinal do sensor de corrente deve ser condicionado para leitura pelo sistema de aquisição.

3.3 Conversão de Sinais

RF08: O sistema deve converter todos os sinais analógicos para formato digital utilizando conversores A/D do microcontrolador ou externos se necessário.

RF09: A resolução da conversão deve ser suficiente para garantir precisão adequada das medições (Ex.: 12 bits).

3.4 Processamento de Dados

RF10: O sistema deve processar os dados adquiridos, aplicando por exemplo: Filtragem de ruído, conversão para unidades físicas (°C e A).

RF11: O sistema deve validar os dados adquiridos, identificando possíveis falhas de sensores.

3.5 Comunicação CAN

RF12: O sistema deve transmitir os dados processados via rede CAN.

RF13: As mensagens CAN devem possivelmente conter: Valor medido, timestamp ou sequência de leitura, identificação do sensor.

RF14: O sistema deve suportar integração com o restante do sistema de controle embarcado via protocolo CAN.

RF15: A taxa de transmissão deve ser configurável conforme necessidade do sistema.

### 4. Requisitos Não Funcionais

RNF01: O sistema deve atualizar as medições com uma frequência mínima.

RNF02: A latência entre aquisição e transmissão não deve exceder o valor a definir.

RNF03: O sistema deve operar de forma contínua durante toda a operação do barco.

RNF04: O sistema deve ser robusto a interferências eletromagnéticas (EMI/EMC), típicas de ambientes com conversores e motores elétricos.

RNF05: O sistema deve detectar falhas nos sensores e comunicar estados de erro via CAN.

RNF06: O sistema deve possuir proteção contra surtos e ruídos elétricos.

RNF07: A medição de temperatura deve ter precisão mínima a definir.

RNF08: A medição de corrente deve ter erro máximo do valor medido a definir.

RNF09: As mensagens devem seguir um formato padronizado e documentado.

RNF10: O sistema deve ter baixo consumo energético para não afetar a autonomia do barco.

RNF11: O sistema deve suportar: Umidade elevada, vibração mecânica, temperaturas variáveis, corrosão.

RNF12: O sistema deve permitir fácil substituição dos sensores.

RNF13: O firmware deve permitir atualização para melhorias futuras.

### 5. Restrições funcionais

RST01: Deve-se usar o sensor de temperatura PT100.

RST02: Deve-se usar o sensor de corrente de efeito hall de 600 A.

RST03: A versão do protocolo CAN deve ser a versão atual do barco.

RST04: O firmware deve ser escrito na linguagem de programação C.

RST05: O microcontrolador usado deve ser o ATMega 328p.

### 6. Considerações Finais

O sistema proposto visa garantir monitoramento confiável e em tempo real de variáveis críticas para operação segura e eficiente de um barco movido a energia solar, contribuindo para proteção dos equipamentos e otimização do desempenho energético.

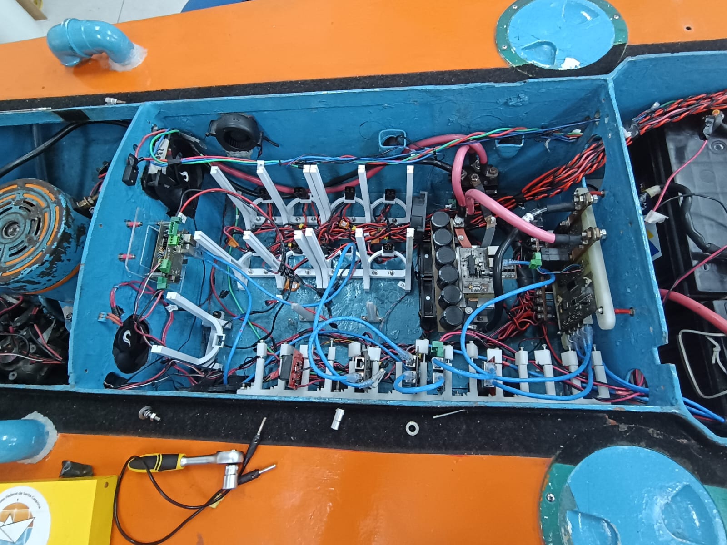
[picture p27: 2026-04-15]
etapa_1/images/loadCdiv.png

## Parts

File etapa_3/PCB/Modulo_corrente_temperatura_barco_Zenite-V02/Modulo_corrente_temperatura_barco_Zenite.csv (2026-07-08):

Reference | Qty | Value | DNP | Exclude from BOM | Exclude from Board | Footprint | Datasheet
C1 | 1 | 10uF |  |  |  | Capacitor_THT:CP_Radial_D6.3mm_P2.50mm
C2 | 1 | 470pF |  |  |  | Capacitor_SMD:C_0805_2012Metric_Pad1.18x1.45mm_HandSolder
C3 | 1 | 220nF |  |  |  | Capacitor_SMD:C_0805_2012Metric_Pad1.18x1.45mm_HandSolder
C4,C5,C8,C11 | 4 | 100nF |  |  |  | Capacitor_SMD:C_0805_2012Metric_Pad1.18x1.45mm_HandSolder
C6 | 1 | 1nF |  |  |  | Capacitor_SMD:C_0805_2012Metric_Pad1.18x1.45mm_HandSolder
C9,C10 | 2 | 22pF |  |  |  | Capacitor_SMD:C_0805_2012Metric_Pad1.18x1.45mm_HandSolder
C12,C13 | 2 | 100uF |  |  |  | Capacitor_THT:CP_Radial_D6.3mm_P2.50mm
C_Low_pass1 | 1 | x pF |  |  |  | Capacitor_SMD:C_0805_2012Metric_Pad1.18x1.45mm_HandSolder
D1 | 1 | D |  |  |  | Diode_THT:D_5W_P10.16mm_Horizontal
D2 | 1 | D_Zener |  |  |  | Diode_THT:D_5W_P10.16mm_Horizontal
D3 | 1 | PRTR5V0U2X |  |  |  | Package_TO_SOT_SMD:SOT-143_Handsoldering | https://assets.nexperia.com/documents/data-sheet/PRTR5V0U2X.pdf
D4,D5 | 2 | D_Zener |  |  |  | Diode_SMD:D_SOD-123
F1 | 1 | Fuse |  |  |  | pi-III-lib:fuse_holder
J1,J2 | 2 | RJ45_Shielded |  |  |  | pi-III-lib:TE_RJ45-8N-B
J3 | 1 | 2edgrc |  |  |  | pi-III-lib:2EDRC_4pins
L1 | 1 | 5u6H |  |  |  | pi-III-lib:ASPI0630LR5R6MT15
MAX1,MAX2,MAX3 | 3 | max31865_adafruit |  |  |  | pi-III-lib:max31868_module
MIC1 | 1 | STM32F401 |  |  |  | pi-III-lib:BlackPill
PS1 | 1 | RS3K-2412DZ_H3 |  |  |  | pi-III-lib:RS3K2412DZH3 | https://recom-power.com/pdf/Econoline/RS3K(-Z).pdf
R1,R2,R3 | 3 | 100k |  |  |  | Resistor_THT:R_Axial_DIN0207_L6.3mm_D2.5mm_P10.16mm_Horizontal
R4,R5,R6,R7,R9,R10 | 6 | 100k |  |  |  | Resistor_SMD:R_1206_3216Metric_Pad1.30x1.75mm_HandSolder
R8,R14 | 2 | 33 |  |  |  | Resistor_SMD:R_1206_3216Metric_Pad1.30x1.75mm_HandSolder
R13 | 1 | 4k7 |  |  |  | Resistor_SMD:R_0805_2012Metric_Pad1.20x1.40mm_HandSolder
R15 | 1 | 0R |  |  |  | Resistor_SMD:R_0805_2012Metric_Pad1.20x1.40mm_HandSolder
R_Low_pass1 | 1 | xk |  |  |  | Resistor_SMD:R_0805_2012Metric_Pad1.20x1.40mm_HandSolder
U2 | 1 | LM7805 |  |  |  | Package_TO_SOT_THT:TO-220-3_Horizontal_TabDown | https://www.onsemi.cn/PowerSolutions/document/MC7800-D.PDF
U3 | 1 | TLV2376IDGKR |  |  |  | Package_SO:VSSOP-8_3x3mm_P0.65mm
U4 | 1 | MCP2515-xSO |  |  |  | Package_SO:SOIC-18W_7.5x11.6mm_P1.27mm | http://ww1.microchip.com/downloads/en/DeviceDoc/21801e.pdf
U5 | 1 | MCP2551-I-SN |  |  |  | Package_SO:SOIC-8_3.9x4.9mm_P1.27mm | http://ww1.microchip.com/downloads/en/devicedoc/21667d.pdf
Y1 | 1 | 16MHz |  |  |  | Crystal:Crystal_HC50_Vertical

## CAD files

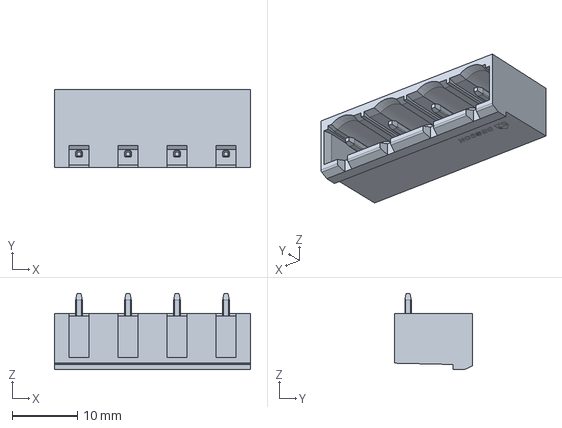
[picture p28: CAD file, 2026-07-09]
etapa_3/PCB/Modulo_corrente_temperatura_barco_Zenite-V02/models/2EDGRC-7.5-04P-1Y-100A&Z(H).stp
30.0 x 12.0 x 11.7 mm

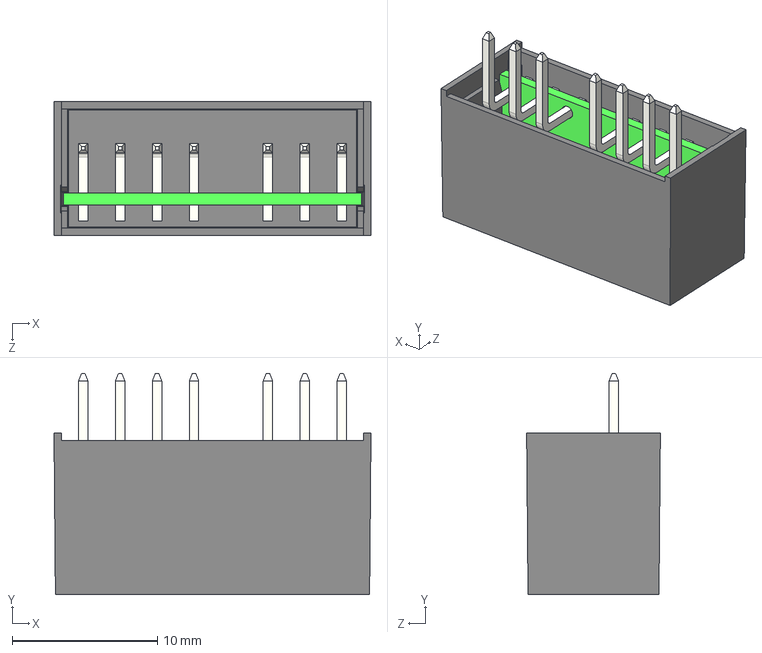
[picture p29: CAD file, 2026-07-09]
etapa_3/PCB/Modulo_corrente_temperatura_barco_Zenite-V02/models/RS3K-2412DZ_H3.STEP
21.8 x 15.2 x 9.20 mm

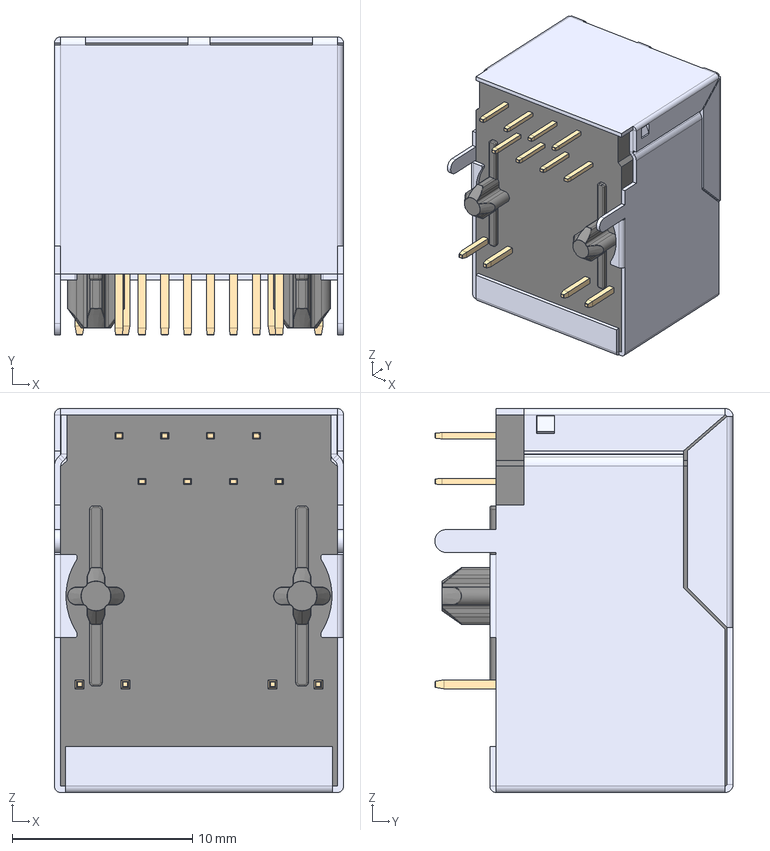
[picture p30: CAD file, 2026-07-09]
etapa_3/PCB/Modulo_corrente_temperatura_barco_Zenite-V02/models/hanrun_HR911105A_socket.step
16.0 x 16.6 x 21.3 mm
HR911105A_yellow_led
HR911105A_pin_001
HR911105A_pin_002
HR911105A_pin_003
HR911105A_pin_004
HR911105A_pin_005
HR911105A_pin_006
HR911105A_pin_007
HR911105A_pin_008
HR911105A_pin_009
HR911105A_pin_010
HR911105A_contact_004
HR911105A_contact_003
HR911105A_contact_002
HR911105A_contact_001
HR911105A_red_led
HR911105A_pin_011
HR911105A_pin_012
HR911105A_contact_005
HR911105A_contact_006
HR911105A_contact_007
HR911105A_contact_008
HR911105A_outer_shield
HR911105A_inner_023

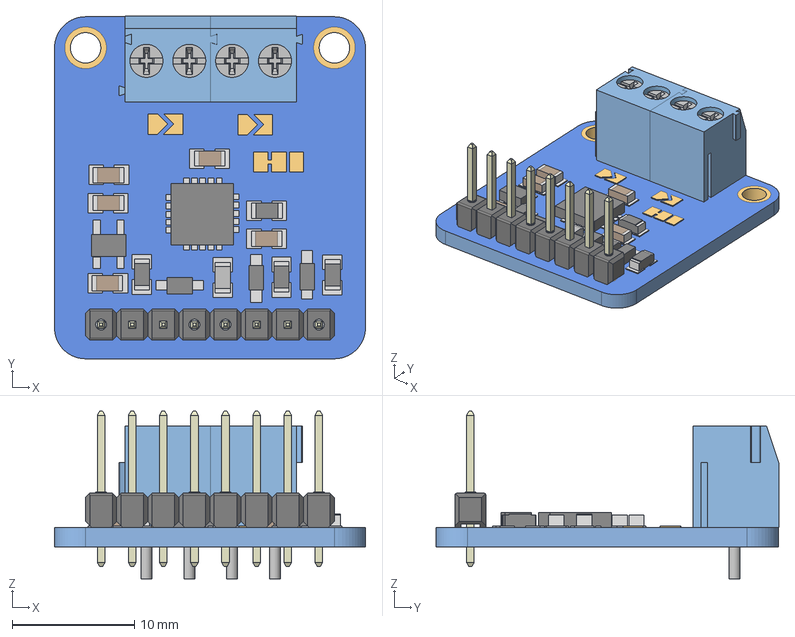
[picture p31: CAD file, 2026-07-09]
etapa_3/PCB/Modulo_corrente_temperatura_barco_Zenite-V02/models/MAX31865.stp
25.4 x 28.0 x 13.7 mm
plytka
Pin Header 1x4 TH Pitch 2.54mm x 2
TE_1776275-2 x 2

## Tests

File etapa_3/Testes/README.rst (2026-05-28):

Testes
#######

.. contents::
   :local:
   :depth: 2

Visão geral
***********

Esse diretório contém os códigos usados durante o teste dos drivers e hardwares.

Testes
======

Foram testados ambos os controladores e transmissores CAN via SPI utilizando o `Blackpill <pi3_CAN_test>`_ como transmissor e o `ESP32 <ESP32devkit/ESP32MCP2515>`_ como receptor de teste.

Também foram testadas as tarefas no FreeRTOS para facilitar a temporização e escalonamento das tarefas de sensoriamento e comunicação.

Imagem de teste do `Transmissor CAN </etapa_3/Testes/CAN_Module/Src>`_ onde foi observado o envio da corrente e o pacote recebido.

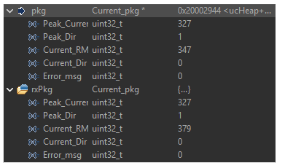
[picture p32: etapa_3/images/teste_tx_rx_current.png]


Foi montada uma placa perfurada de cobre para testar a transmissão.

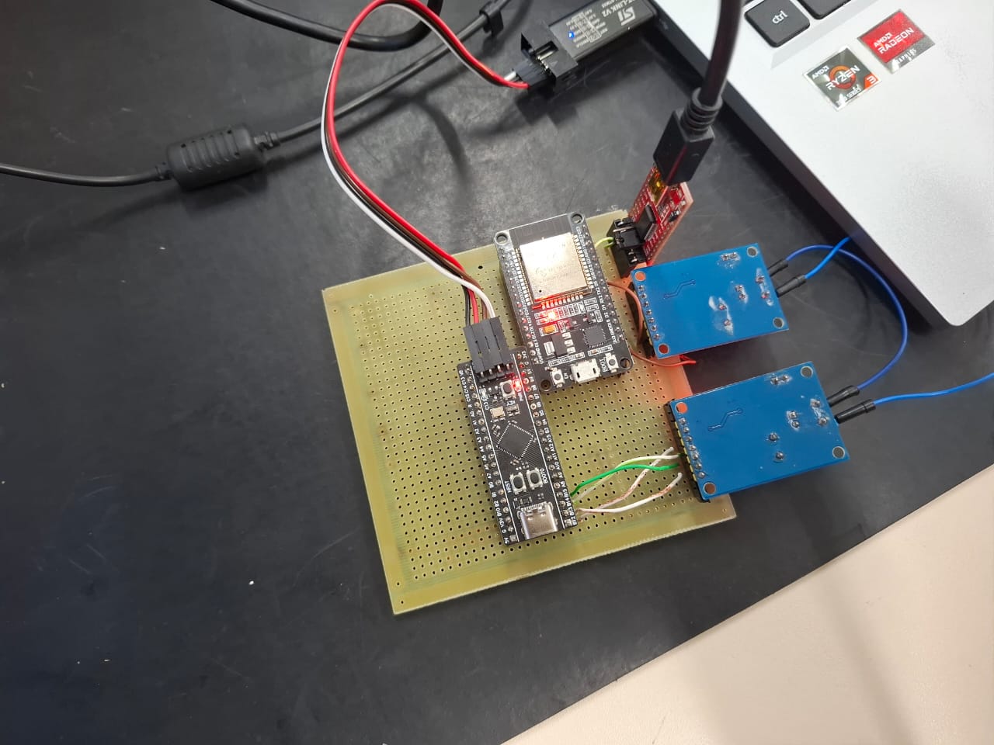
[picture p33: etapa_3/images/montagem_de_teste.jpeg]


Na imagem temos o Blackpill conectado via SPI2 ao MCP2515 (tx) e um ESP32 conectado via SPI no MCP2515 (rx).

Sequência de funcionamento das tarefas
======
`Corrente <Sensor_RTOS/Core/Src/current_task.c#L21-42>`_ ::

   DMA callback (Half/Full)
      ↓
   CurrentTask
      ↓
   Treated buffer ready
      ↓
   CANCurrentTask wakes up
      ↓
   Calculate RMS
      ↓
   send via CAN

`Temperatura <Sensor_RTOS/Core/Src/rtd_task.c#L24-48>`_::

   TIM3 ISR trigger
      ↓
   RTDTask
      ↓
   Temperatures updated
      ↓
   CANTempTask wakes up
      ↓
   send via CAN

Pinout do ESP32

============ ==========  
MCP2515 Pin  ESP32 Pin 
============ ==========
VCC 	       5V
GND 	       GND
CS 	       IO5
SO 	       IO19
SI 	       IO23
SCK 	       IO13
INT 	       IO4
============ ==========

Referências
*************************************

- `Código de interface MCP2515 <https://github.com/eziya/STM32_SPI_MCP2515/tree/master>`_

- `Tutorial de setup do MCP2515 para o ESP32 <https://how2electronics.com/esp32-can-bus-communication-with-mcp2515-module/>`_

- `Driver do MCP2515 para o ESP32 <https://github.com/autowp/arduino-mcp2515/>`_

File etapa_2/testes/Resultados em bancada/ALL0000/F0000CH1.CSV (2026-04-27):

Record Length | 2.500000e+03 | -0.002500000000 | -0.15200
Sample Interval | 2.000000e-06 | -0.002498000000 | -0.13200
Trigger Point | 1.250000000000e+03 | -0.002496000000 | -0.16000
 |  | -0.002494000000 | -0.14000
 |  | -0.002492000000 | -0.15600
 |  | -0.002490000000 | -0.14000
Source | CH1 | -0.002488000000 | -0.14800
Vertical Units | V | -0.002486000000 | -0.14400
Vertical Scale | 1.000000e-01 | -0.002484000000 | -0.15200
Vertical Offset | 0.000000e+00 | -0.002482000000 | -0.14800
Horizontal Units | s | -0.002480000000 | -0.16800
Horizontal Scale | 5.000000e-04 | -0.002478000000 | -0.14000
Pt Fmt | Y | -0.002476000000 | -0.14400
Yzero | 0.000000e+00 | -0.002474000000 | -0.14800
Probe Atten | 1.000000e+01 | -0.002472000000 | -0.15200
Model Number | TBS1062 | -0.002470000000 | -0.16400
Serial Number | C020573 | -0.002468000000 | -0.13600
Firmware Version | FV:v26.02 | -0.002466000000 | -0.15200
 |  | -00.002464000000 | -0.16800
 |  | -00.002462000000 | -0.16000
 |  | -00.002460000000 | -0.14800
 |  | -00.002458000000 | -0.16000
 |  | -00.002456000000 | -0.13200
 |  | -00.002454000000 | -0.14800
 |  | -00.002452000000 | -0.15600
 |  | -00.002450000000 | -0.15200
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

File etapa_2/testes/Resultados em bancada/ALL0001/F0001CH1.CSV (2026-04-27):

Record Length | 2.500000e+03 | -0.002500000000 | 0.13600
Sample Interval | 2.000000e-06 | -0.002498000000 | 0.14800
Trigger Point | 1.250000000000e+03 | -0.002496000000 | 0.16000
 |  | -0.002494000000 | 0.14800
 |  | -0.002492000000 | 0.14000
 |  | -0.002490000000 | 0.16000
Source | CH1 | -0.002488000000 | 0.15600
Vertical Units | V | -0.002486000000 | 0.14000
Vertical Scale | 1.000000e-01 | -0.002484000000 | 0.15200
Vertical Offset | 0.000000e+00 | -0.002482000000 | 0.14400
Horizontal Units | s | -0.002480000000 | 0.15200
Horizontal Scale | 5.000000e-04 | -0.002478000000 | 0.14800
Pt Fmt | Y | -0.002476000000 | 0.15200
Yzero | 0.000000e+00 | -0.002474000000 | 0.15600
Probe Atten | 1.000000e+01 | -0.002472000000 | 0.14800
Model Number | TBS1062 | -0.002470000000 | 0.16800
Serial Number | C020573 | -0.002468000000 | 0.14400
Firmware Version | FV:v26.02 | -0.002466000000 | 0.14400
 |  | -00.002464000000 | 0.14400
 |  | -00.002462000000 | 0.16000
 |  | -00.002460000000 | 0.16000
 |  | -00.002458000000 | 0.14800
 |  | -00.002456000000 | 0.14800
 |  | -00.002454000000 | 0.14000
 |  | -00.002452000000 | 0.14400
 |  | -00.002450000000 | 0.16000
 |  | -00.002448000000 | 0.15200
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

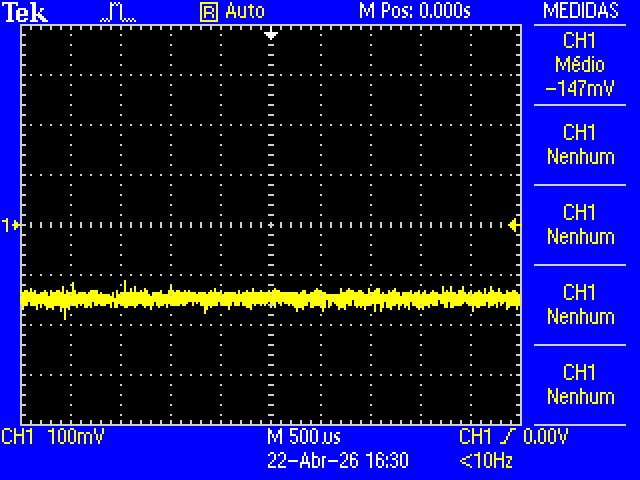
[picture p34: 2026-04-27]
etapa_2/testes/Resultados em bancada/ALL0000/F0000TEK.JPG

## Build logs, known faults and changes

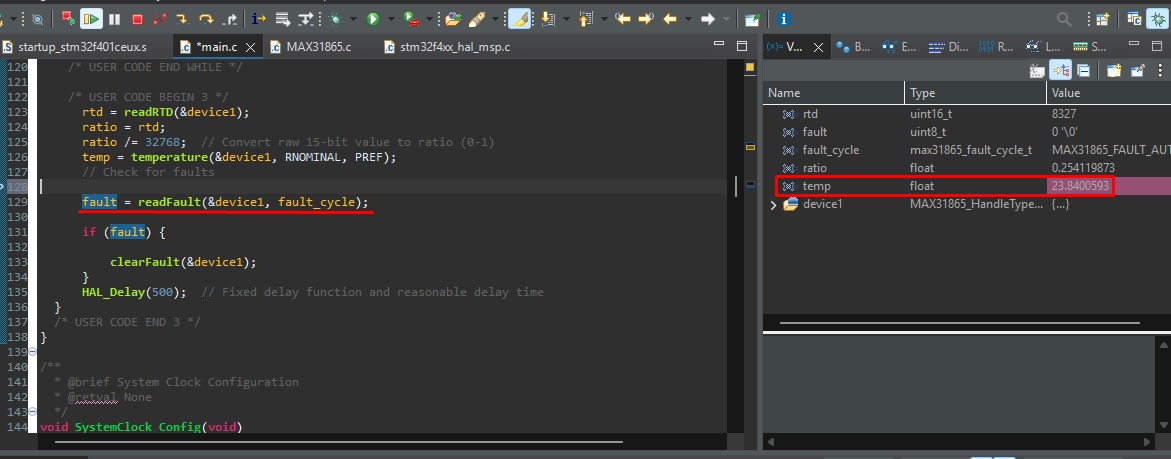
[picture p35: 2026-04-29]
etapa_2/images/Pt100/debugger1.jpeg

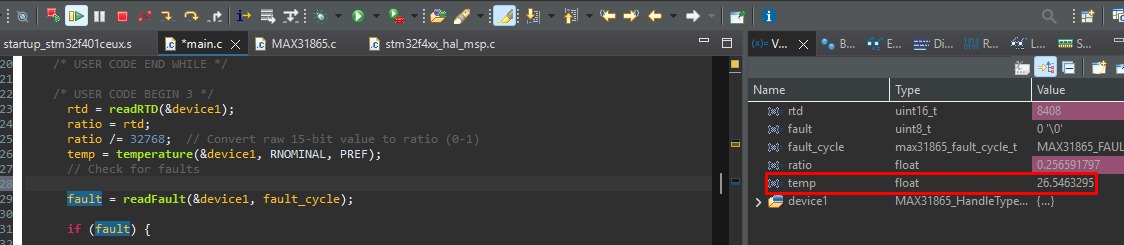
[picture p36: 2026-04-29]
etapa_2/images/Pt100/debugger2.jpeg

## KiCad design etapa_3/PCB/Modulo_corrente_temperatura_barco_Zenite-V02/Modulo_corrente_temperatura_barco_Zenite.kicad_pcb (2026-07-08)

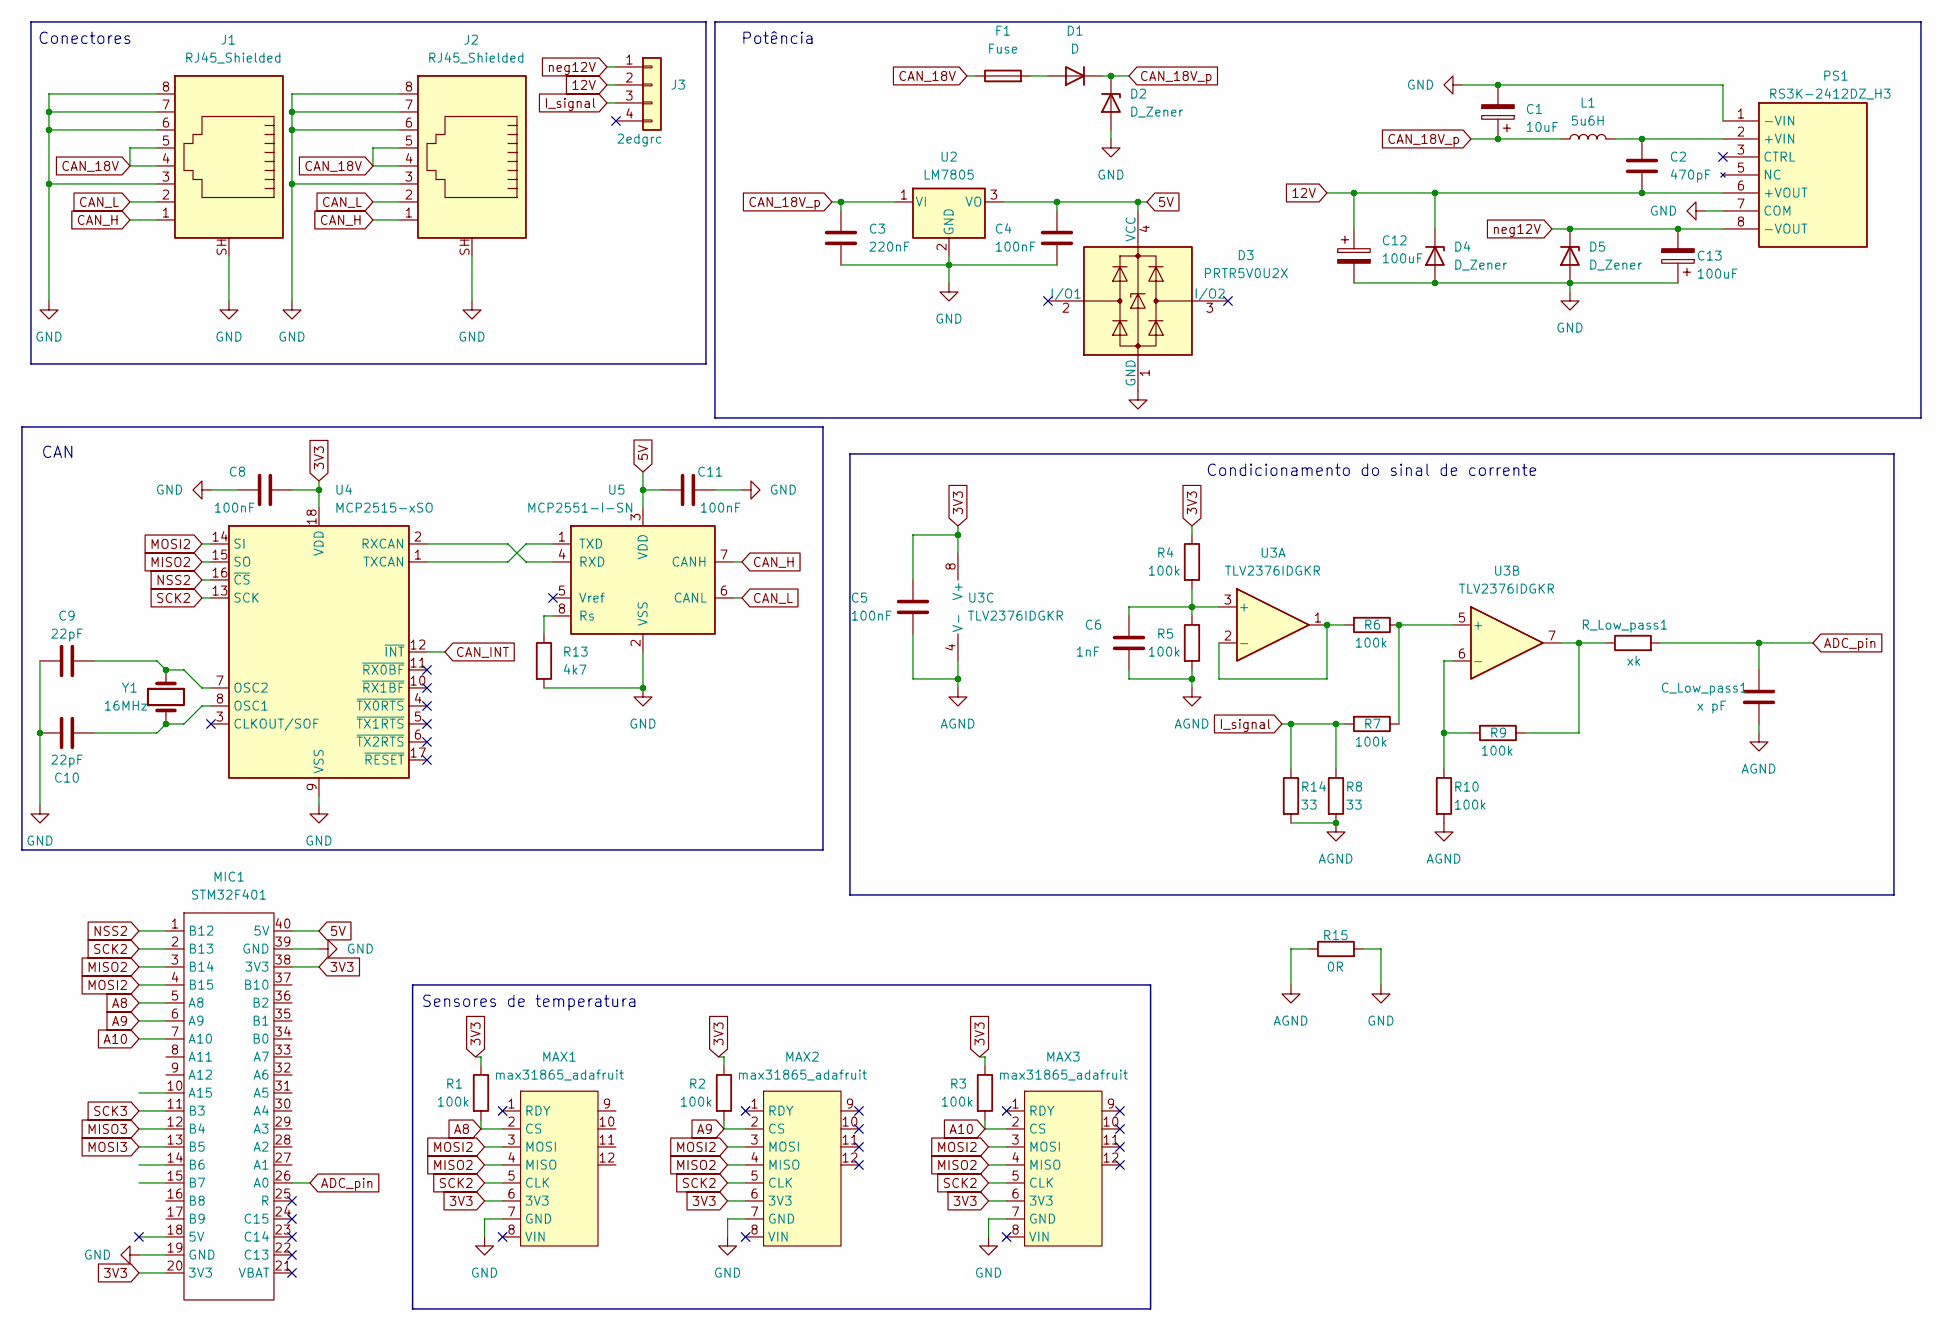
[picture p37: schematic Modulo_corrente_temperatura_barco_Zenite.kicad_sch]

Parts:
C1: 10uF; CP_Radial_D6.3mm_P2.50mm
C2: 470pF; C_0805_2012Metric_Pad1.18x1.45mm_HandSolder
C3: 220nF; C_0805_2012Metric_Pad1.18x1.45mm_HandSolder
C4, C5, C8, C11: 100nF; C_0805_2012Metric_Pad1.18x1.45mm_HandSolder
C6: 1nF; C_0805_2012Metric_Pad1.18x1.45mm_HandSolder
C9, C10: 22pF; C_0805_2012Metric_Pad1.18x1.45mm_HandSolder
C12, C13: 100uF; CP_Radial_D6.3mm_P2.50mm
C_Low_pass1: x pF; C_0805_2012Metric_Pad1.18x1.45mm_HandSolder
D1: D; D_5W_P10.16mm_Horizontal
D2: D_Zener; D_5W_P10.16mm_Horizontal
D3: PRTR5V0U2X; SOT-143_Handsoldering
D4, D5: D_Zener; D_SOD-123
F1: Fuse; fuse_holder
J1, J2: RJ45_Shielded; TE_RJ45-8N-B
J3: 2edgrc; 2EDRC_4pins
L1: 5u6H; ASPI0630LR5R6MT15
MAX1, MAX2, MAX3: max31865_adafruit; max31868_module
MIC1: STM32F401; BlackPill
PS1: RS3K-2412DZ_H3; RS3K2412DZH3; Manufacturer_Part_Number RS3K-2412DZ/H3
R1, R2, R3: 100k; R_Axial_DIN0207_L6.3mm_D2.5mm_P10.16mm_Horizontal
R4, R5, R6, R7, R9, R10: 100k; R_1206_3216Metric_Pad1.30x1.75mm_HandSolder
R8, R14: 33; R_1206_3216Metric_Pad1.30x1.75mm_HandSolder
R13: 4k7; R_0805_2012Metric_Pad1.20x1.40mm_HandSolder
R15: 0R; R_0805_2012Metric_Pad1.20x1.40mm_HandSolder
R_Low_pass1: xk; R_0805_2012Metric_Pad1.20x1.40mm_HandSolder
U2: LM7805; TO-220-3_Horizontal_TabDown
U3: TLV2376IDGKR; VSSOP-8_3x3mm_P0.65mm
U4: MCP2515-xSO; SOIC-18W_7.5x11.6mm_P1.27mm
U5: MCP2551-I-SN; SOIC-8_3.9x4.9mm_P1.27mm
Y1: 16MHz; Crystal_HC50_Vertical

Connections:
3V3: C5.1, C8.2, MAX1.6 (3V3), MAX2.6 (3V3), MAX3.6 (3V3), MIC1.20 (3V3), MIC1.38 (3V3), R1.1, R2.1, R3.1, R4.1, U3.8 (V+), U4.18 (VDD)
5V: C4.1, C11.1, D3.4 (VCC), MIC1.40 (5V), U2.3 (VO), U5.3 (VDD)
12V: C2.2, C12.1, D4.1 (K), J3.2, PS1.6 (+VOUT)
A8: MAX1.2 (CS), MIC1.5 (A8), R1.2
A9: MAX2.2 (CS), MIC1.6 (A9), R2.2
A10: MAX3.2 (CS), MIC1.7 (A10), R3.2
ADC_pin: C_Low_pass1.1, MIC1.26 (A0), R_Low_pass1.2
AGND: C5.2, C6.2, C_Low_pass1.2, R5.2, R8.2, R10.2, R14.2, R15.1, U3.4 (V-)
CAN_18V: F1.1, J1.4, J1.5, J2.4, J2.5
CAN_18V_p: C1.1, C3.1, D1.1 (K), D2.1 (K), L1.1, U2.1 (VI)
CAN_H: J1.1, J2.1, U5.7 (CANH)
CAN_INT: U4.12 (~INT)
CAN_L: J1.2, J2.2, U5.6 (CANL)
GND: C1.2, C3.2, C4.2, C8.1, C9.1, C10.1, C11.2, C12.2, C13.1, D2.2 (A), D3.1 (GND), D4.2 (A), D5.2 (A), J1.3, J1.6, J1.7, J1.8, J1.SH, J2.3, J2.6, J2.7, J2.8, J2.SH, MAX1.7 (GND), MAX2.7 (GND), MAX3.7 (GND), MIC1.19 (GND), MIC1.39 (GND), PS1.1 (-VIN), PS1.7 (COM), R13.2, R15.2, U2.2 (GND), U4.9 (VSS), U5.2 (VSS)
I_signal: J3.3, R7.2, R8.1, R14.1
MISO2: MAX1.4 (MISO), MAX2.4 (MISO), MAX3.4 (MISO), MIC1.3 (B14), U4.15 (SO)
MISO3: MIC1.12 (B4)
MOSI2: MAX1.3 (MOSI), MAX2.3 (MOSI), MAX3.3 (MOSI), MIC1.4 (B15), U4.14 (SI)
MOSI3: MIC1.13 (B5)
NSS2: MIC1.1 (B12), U4.16 (~CS)
unnamed: D1.2 (A), F1.2
unnamed: C2.1, L1.2, PS1.2 (+VIN)
unnamed: R9.1, R_Low_pass1.1, U3.7
unnamed: C6.1, R4.2, R5.1, U3.3 (+)
unnamed: R6.2, U3.1, U3.2 (-)
unnamed: R6.1, R7.1, U3.5 (+)
unnamed: R9.2, R10.1, U3.6 (-)
unnamed: C10.2, U4.8 (OSC1), Y1.1
unnamed: C9.2, U4.7 (OSC2), Y1.2
unnamed: U4.2 (RXCAN), U5.4 (RXD)
unnamed: U4.1 (TXCAN), U5.1 (TXD)
unnamed: R13.1, U5.8 (Rs)
SCK2: MAX1.5 (CLK), MAX2.5 (CLK), MAX3.5 (CLK), MIC1.2 (B13), U4.13 (SCK)
SCK3: MIC1.11 (B3)
neg12V: C13.2, D5.1 (K), J3.1, PS1.8 (-VOUT)

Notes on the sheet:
Sensores de temperatura
Conectores
CAN
Condicionamento do sinal de corrente
Potência

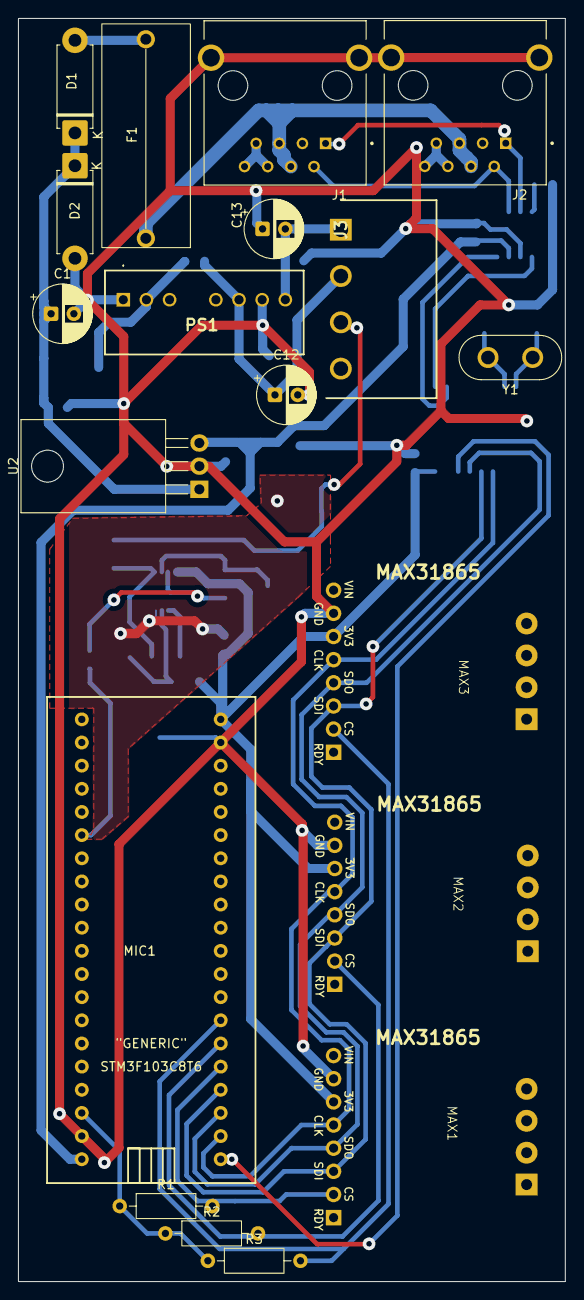
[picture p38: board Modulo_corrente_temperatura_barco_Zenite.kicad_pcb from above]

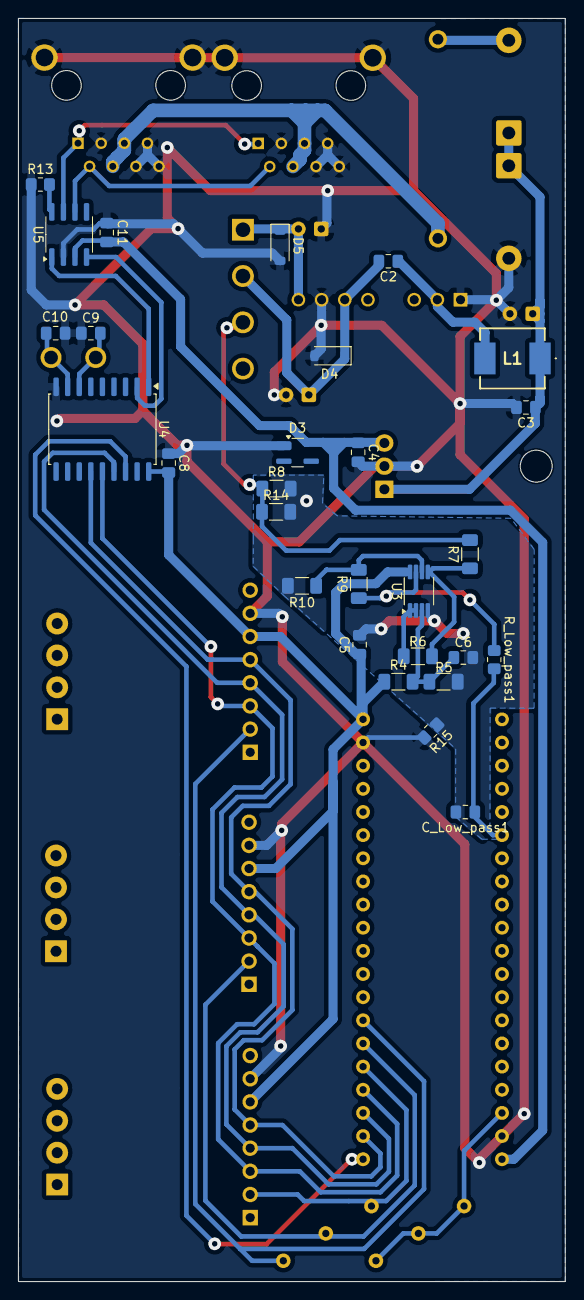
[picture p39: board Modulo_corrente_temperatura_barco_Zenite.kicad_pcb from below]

Board: 2 copper layers, 60.0 x 138.6 mm, 47 parts (28 on the bottom side), 31 nets.

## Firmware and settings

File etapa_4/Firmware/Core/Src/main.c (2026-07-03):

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
/* Includes ------------------------------------------------------------------*/
#include "main.h"
#include "cmsis_os.h"

/* USER CODE BEGIN Includes */
#include "current_sensor.h"
#include "temperature_sensor.h"
#include "CANSPI.h"
#include "MCP2515.h"
/* USER CODE END Includes */

ADC_HandleTypeDef hadc1;
DMA_HandleTypeDef hdma_adc1;

SPI_HandleTypeDef hspi1;
SPI_HandleTypeDef hspi2;

TIM_HandleTypeDef htim2;
TIM_HandleTypeDef htim3;

/* Definitions for defaultTask */
osThreadId_t defaultTaskHandle;
const osThreadAttr_t defaultTask_attributes = {
  .name = "defaultTask",
  .stack_size = 128 * 4,
  .priority = (osPriority_t) osPriorityNormal,
};
/* USER CODE BEGIN PV */
osThreadId_t rtdTaskHandle;
osThreadId_t currentTaskHandle;
osThreadId_t canTempTaskHandle;
osThreadId_t canCurrentTaskHandle;

osMessageQueueId_t current_queue;
osMessageQueueId_t temp_queue;

uint16_t adc_buffer[DMA_BUFF_LENGTH];

const osThreadAttr_t rtdTask_attributes = {
    .name = "rtdTask",
    .stack_size = 256 * 4,
    .priority = (osPriority_t) osPriorityNormal,
};

const osThreadAttr_t currentTask_attributes = {
    .name = "currentTask",
    .stack_size = 256 * 4,
    .priority = (osPriority_t) osPriorityAboveNormal,
};

const osThreadAttr_t canTempTask_attributes = {
    .name = "canTempTask",
    .stack_size = 256 * 4,
    .priority = (osPriority_t) osPriorityLow,
};

const osThreadAttr_t canCurrentTask_attributes = {
    .name = "canCurrentTask",
    .stack_size = 256 * 4,
    .priority = (osPriority_t) osPriorityLow,
};

/* USER CODE END PV */

void SystemClock_Config(void);
static void MX_GPIO_Init(void);
static void MX_DMA_Init(void);
static void MX_ADC1_Init(void);
static void MX_SPI1_Init(void);
static void MX_TIM2_Init(void);
static void MX_TIM3_Init(void);
static void MX_SPI2_Init(void);
void StartDefaultTask(void *argument);

/**
  * @brief  The application entry point.
  * @retval int
  */
int main(void)
{

  /* MCU Configuration--------------------------------------------------------*/

  /* Reset of all peripherals, Initializes the Flash interface and the Systick. */
  HAL_Init();

  /* Configure the system clock */
  SystemClock_Config();

  /* Initialize all configured peripherals */
  MX_GPIO_Init();
  MX_DMA_Init();
  MX_ADC1_Init();
  MX_SPI1_Init();
  MX_TIM2_Init();
  MX_TIM3_Init();
  MX_SPI2_Init();
  /* USER CODE BEGIN 2 */
  RTD_Init();

  if (!CANSPI_Initialize()){
	  Error_Handler();
  }

  /* USER CODE END 2 */

  /* Init scheduler */
  osKernelInitialize();

  /* USER CODE BEGIN RTOS_MUTEX */
  /* add mutexes, ... */
  /* USER CODE END RTOS_MUTEX */

  /* USER CODE BEGIN RTOS_SEMAPHORES */
  /* add semaphores, ... */
  /* USER CODE END RTOS_SEMAPHORES */

  /* USER CODE BEGIN RTOS_TIMERS */
  /* start timers, add new ones, ... */
  /* USER CODE END RTOS_TIMERS */

  /* USER CODE BEGIN RTOS_QUEUES */
  /* add queues, ... */
  current_queue = osMessageQueueNew(CURRENT_QUEUE_LENGTH, sizeof(uint32_t[DMA_BUFF_LENGTH]), NULL);

  temp_queue = osMessageQueueNew(TEMP_QUEUE_LENGTH , sizeof(tempData_t[3]), NULL);

  /* USER CODE END RTOS_QUEUES */

  /* Create the thread(s) */
  /* creation of defaultTask */
  defaultTaskHandle = osThreadNew(StartDefaultTask, NULL, &defaultTask_attributes);

  /* USER CODE BEGIN RTOS_THREADS */
  /* add threads, ... */
  rtdTaskHandle = osThreadNew(RTDTask, NULL, &rtdTask_attributes);

  currentTaskHandle = osThreadNew(CurrentTask, NULL, &currentTask_attributes);

  canTempTaskHandle = osThreadNew(CANTempTask, NULL, &canTempTask_attributes);

  canCurrentTaskHandle = osThreadNew(CANCurrentTask, NULL, &canCurrentTask_attributes);


  /* USER CODE END RTOS_THREADS */

  /* USER CODE BEGIN RTOS_EVENTS */
  /* add events, ... */
  HAL_TIM_PWM_Start(&htim2, TIM_CHANNEL_1);
  HAL_TIM_Base_Start_IT(&htim3);
  HAL_ADC_Start_DMA(&hadc1, (uint32_t*)adc_buffer, DMA_BUFF_LENGTH);
  /* USER CODE END RTOS_EVENTS */

  /* Start scheduler */
  osKernelStart();

  /* We should never get here as control is now taken by the scheduler */

  /* Infinite loop */
  /* USER CODE BEGIN WHILE */
  while (1)
  {
    /* USER CODE END WHILE */

    /* USER CODE BEGIN 3 */
  }
  /* USER CODE END 3 */
}

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
/* USER CODE BEGIN 4 */
void HAL_ADC_ConvHalfCpltCallback(ADC_HandleTypeDef* hadc){
	osThreadFlagsSet(currentTaskHandle, ADC_HALF_READY);
}
void HAL_ADC_ConvCpltCallback(ADC_HandleTypeDef* hadc){
	osThreadFlagsSet(currentTaskHandle, ADC_FULL_READY);
}
/* USER CODE END 4 */

/* USER CODE BEGIN Header_StartDefaultTask */
/**
  * @brief  Function implementing the defaultTask thread.
  * @param  argument: Not used
  * @retval None
  */
/* USER CODE END Header_StartDefaultTask */
void StartDefaultTask(void *argument)
{
  /* USER CODE BEGIN 5 */
  /* Infinite loop */
  for(;;)
  {
    HAL_GPIO_TogglePin(LED_GPIO_Port, LED_Pin);
    osDelay(1000);
  }
  /* USER CODE END 5 */
}

/**
  * @brief  Period elapsed callback in non blocking mode
  * @note   This function is called  when TIM4 interrupt took place, inside
  * HAL_TIM_IRQHandler(). It makes a direct call to HAL_IncTick() to increment
  * a global variable "uwTick" used as application time base.
  * @param  htim : TIM handle
  * @retval None
  */
void HAL_TIM_PeriodElapsedCallback(TIM_HandleTypeDef *htim)
{
  /* USER CODE BEGIN Callback 0 */
	if (htim->Instance == TIM3)
	{
		osThreadFlagsSet(rtdTaskHandle, RTD_READ_FLAG); // every 1 second
	}
  /* USER CODE END Callback 0 */
  if (htim->Instance == TIM4)
  {
    HAL_IncTick();
  }
}

/**
  * @brief  This function is executed in case of error occurrence.
  * @retval None
  */
void Error_Handler(void)
{
  /* USER CODE BEGIN Error_Handler_Debug */
  /* User can add his own implementation to report the HAL error return state */
  __disable_irq();
  uint8_t canstat = MCP2515_ReadByte(MCP2515_CANSTAT);
  uint8_t canctrl = MCP2515_ReadByte(MCP2515_CANCTRL);
  uint8_t eflg    = MCP2515_ReadByte(MCP2515_EFLG);
  __BKPT();
  while (1)
  {
  }
  /* USER CODE END Error_Handler_Debug */
}
#ifdef USE_FULL_ASSERT
/**
  * @brief  Reports the name of the source file and the source line number
  *         where the assert_param error has occurred.
  * @param  file: pointer to the source file name
  * @param  line: assert_param error line source number
  * @retval None
  */
void assert_failed(uint8_t *file, uint32_t line)
{
  /* USER CODE BEGIN 6 */
  /* User can add his own implementation to report the file name and line number,
     ex: printf("Wrong parameters value: file %s on line %d\r\n", file, line) */
  /* USER CODE END 6 */
}
#endif /* USE_FULL_ASSERT */

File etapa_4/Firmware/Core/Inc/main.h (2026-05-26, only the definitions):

#define LED_Pin GPIO_PIN_13
#define LED_GPIO_Port GPIOC
#define CS3_Pin GPIO_PIN_2
#define CS3_GPIO_Port GPIOA
#define CS2_Pin GPIO_PIN_3
#define CS2_GPIO_Port GPIOA
#define CS1_Pin GPIO_PIN_4
#define CS1_GPIO_Port GPIOA
#define CAN_CS_Pin GPIO_PIN_12
#define CAN_CS_GPIO_Port GPIOB

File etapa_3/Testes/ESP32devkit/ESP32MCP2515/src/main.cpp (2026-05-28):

#include <SPI.h>
#include <mcp2515.h>
#include <HardwareSerial.h>
 
struct can_frame canMsg;
struct MCP2515 mcp2515(5); // CS pin is GPIO 5

#define CAN_ID_1 0x010
#define CAN_ID_2 0x011

void setup()
{
  Serial.begin(9600);

  SPI.begin();
 
  mcp2515.reset();
  mcp2515.setBitrate(CAN_500KBPS, MCP_8MHZ);
  mcp2515.setNormalMode();

  //Serial.println("ESP32_configurado/n")
}
 
 
void loop()
{
  if (mcp2515.readMessage(&canMsg) == MCP2515::ERROR_OK)
  {
    if (canMsg.can_id == CAN_ID_1)  // Check if the message is from the sender
    {
      unsigned char data[4];

      for (int i = 0; i<4; i++){
        data[i] = canMsg.data[i];
      }
      

      Serial.println("Data received: ");
      for (int i = 0; i<4; i++){
        Serial.println(data[i]);
        Serial.println((uint8_t)data[i]);
      }
    }
    if (canMsg.can_id == CAN_ID_2)  // Check if the message is from the sender
    {
      unsigned char data[4];

      for (int i = 0; i<4; i++){
        data[i] = canMsg.data[i];
      }
      

      Serial.println("Data received: ");
      for (int i = 0; i<4; i++){
        Serial.println(data[i]);
        Serial.println((uint8_t)data[i]);
      }
    }
  }
}

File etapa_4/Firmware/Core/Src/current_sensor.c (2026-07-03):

/*
 * Current_Sensor.c
 *
 *  Created on: 20 de mai. de 2026
 *      Author: potato
 */

#include "current_sensor.h"
#include <math.h>
#include <string.h>
#include "MCP2515.h"
static uint32_t peak = 0;

static uCAN_MSG txMsg =
{
    .frame =
    {
        .idType = dSTANDARD_CAN_MSG_ID_2_0B,
        .id     = CAN_ID_SENSOR_CORRENTE,
        .dlc    = sizeof(Current_pkg)
    }
};

/**
 * @brief: Extrai valores do ADC e monta pacote
 *
 * Realiza todos os calculos menos o filtro
 *
 * @param: buffer Buffer do ADC
 * @param: lenght Tamanho do buffer
 */
void Mount_Current_Package(uint32_t *buffer, Current_pkg *pkg, uint32_t length){
	int32_t milli_amps = 0;
	int32_t sentido = 0;
	uint64_t acc = 0;

	for(uint32_t i = 0; i<length; i++){

		milli_amps = 125*(((buffer[i]*3300)>>10)-(3300>>1));

		acc += (uint64_t)(milli_amps*milli_amps);

		if (milli_amps > peak){

			peak = milli_amps;
			pkg->Peak_Dir = 1;

		} else if ((-milli_amps) > peak){

			peak = -milli_amps;
			pkg->Peak_Dir = 0;

		}
		if (milli_amps >= 0){
			sentido++;
		} else{
			sentido--;
		}
	}

	if (sentido >= 0){
		pkg->Current_Dir = 1;
	} else{
		pkg->Current_Dir = 0;
	}

	pkg->Error_msg = 0;
	pkg->Peak_Current = (peak/100) & NBIT_MASK(11);
	pkg->Current_RMS = (uint32_t)(sqrt((float)(acc/length))/100) & NBIT_MASK(12);
}

/**
 * @brief: Envia pacote por SPI
 */
void Send_Current_Package(Current_pkg *pkg){
//	Current_pkg rxPkg;
//
//	uCAN_MSG rxMsg;
//

	memcpy(&txMsg.frame.data0, pkg, sizeof(Current_pkg));

	CANSPI_Transmit(&txMsg);

//	if (CANSPI_Receive(&rxMsg))
//	{
//	    memcpy(&rxPkg,
//	           &rxMsg.frame.data0,
//	           sizeof(Current_pkg));
//	}

}

static void IIRFilter(uint16_t *raw, uint32_t *filtered, uint32_t length)
{
    for(uint32_t i = 0; i < length; i++)
    {
    	//TODO: Implementar filtro
    	filtered[i] = raw[i];
    }

}


void CurrentTask(void *argument)
{
    uint32_t flags;
    uint32_t filter_data[DMA_BUFF_LENGTH];

    for(;;)
    {
        flags = osThreadFlagsWait(ADC_HALF_READY | ADC_FULL_READY, osFlagsWaitAny, osWaitForever);

        if(flags & ADC_HALF_READY)
        {
        	IIRFilter(&adc_buffer[0], &filter_data[0], DMA_BUFF_LENGTH/2);
        }

        if(flags & ADC_FULL_READY)
        {
        	IIRFilter(&adc_buffer[DMA_BUFF_LENGTH/2], &filter_data[DMA_BUFF_LENGTH/2], DMA_BUFF_LENGTH/2);

            osMessageQueuePut(current_queue, filter_data, 0, 0);

        }

    }
}

void CANCurrentTask(void *argument)
{
	Current_pkg pkg;
	uint32_t filter_data[DMA_BUFF_LENGTH];

    for(;;)
    {

		if (osMessageQueueGet(current_queue, filter_data, 0, osWaitForever) == osOK)
		{
			Mount_Current_Package(filter_data, &pkg, DMA_BUFF_LENGTH);
			Send_Current_Package(&pkg);
		}

      }
}

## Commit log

2026-03-28 Revise requirements and specifications in README
    Updated functional requirements and specifications for temperature and current measurement, including specific sensor and microcontroller details. Revised signal conversion and CAN communication deta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
2026-03-30 Revise requirements and specifications in README
    Updated functional requirements for temperature and current measurements, including precision and frequency specifications. Enhanced signal conversion and communication details.
2026-03-30 Hall sensor photo
2026-03-30 Update README to include temperature in CAN transmission
2026-03-30 Update README.rst
    etapas de desenvolvimento
2026-03-30 Update README.rst
    flowchart
2026-04-01 Adjust image scales and enhance CAN communication details
    Updated image scales and added details on current measurements in the CAN communication section.
2026-04-15 código de teste para o sensor de temperatura
2026-04-16 refactored for multiple devices
2026-04-24 Update README.rst - Descrição Básica
    Adicionada descrição básica sobre os testes
    Falta:
    - Testar ADC com o sensor e o amplificador
    - Adicionar imagens
    - Detalhar melhor o que foi feito nos laboratórios
    - Testar para correntes negativas com a fonte linear (V < 3.3/2)
2026-04-27 resultados práticos e código funcional
    [F0000CH1.CSV, F0001CH1.CSV]
2026-04-29 Update README.rst
    Adicionados detalhes do teste do sensor ADC - junto com cálculos básicos e imagens dos resultados
2026-04-29 Fix formatting of current values in README
2026-04-30 Update README.rst
    Melhoras na descrição dos testes e implementação do sensor de corrente
2026-04-30 Update main.c
    Bit shift corrigido para dividir - medida de corrente espelhada para o primário
    [main.c]
2026-04-30 Fix typos in README.rst
    Corrige a palavra 'referênte' para 'referente' e remove espaço extra na seção de Desenvolvimento.
2026-05-02 Preliminary module schematic added
    [Modulo_corrente_temperatura_barco_Zenite.kicad_pcb, Modulo_corrente_temperatura_barco_Zenite.kicad_sch]
2026-05-02 sallen-key filter fixed to match 0.707 quality factor
    [Modulo_corrente_temperatura_barco_Zenite.kicad_sch]
2026-05-10 Primeiro Protótipo da Comunicação dos Sensores
    Código ainda não foi testado devido à problemas locais com a geração/compilação de código, provavelmente devido à má configuração do CubeIDE e do CubeMX
    [MAX31865.c, MCP2515.c]
2026-05-10 Update README.rst
    Adicionada referência do código SPI->MCP2515
2026-05-11 MCP2515_driver and code for test added
    [Modulo_corrente_temperatura_barco_Zenite.kicad_sch]
2026-05-11 Fix TX buffer selection and update transmission data
    [MCP2515_driver.c]
2026-05-12 can tasks wireframes
2026-05-13 Update MCP2515.c
    Troacado de SPI1 para SPI2
2026-05-13 Update Sensors.c
    Adicionada linha para transmitir pacote por CAN
2026-05-13 esp32 arduino can receiver build
2026-05-14 esp32 serial print
2026-05-20 Implementados Sensores em RTOS
    Adicionados arquivos dos sensores de corrente e temperatura, incluindo montar os pacotes.
    Falta implementar o protocolo CAN
2026-05-21 obfuscated tasks into their drivers, implemented queues
2026-05-21 Mount pkg and send via SPI functions added for sensors libs
2026-05-21 Projeto Inicial do Filtro
    Cálculo dos coeficientes de um filtro butter, com simulação do resultado final e coeficientes do filtro em SOS para aplicação por CMSIS
2026-05-21 CAN device handle integration
2026-05-23 Adicionado FFT do filtro
    Adicionado plot do FFT do filtro butterworth nas frequências que serão medidas
2026-05-23 Update README.rst
    Adicionado esqueleto do teste da rede CAN
    - Comparativo entre dados enviados e recebidos
    - Detalhes sobre a placa
    - Falar sobre a implementação dos sensores de corrente e temperatura, incluindo cálculos
    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
2026-05-24 Document CAN protocol and sensor integration
    Added documentation for CAN protocol implementation and sensor data integration.
2026-05-24 update README with Schematics and performance criteria
2026-05-24 Ajustar referências e texto no README
    Corrigido o formato das referências aos arquivos de código e melhorada a clareza do texto.
2026-05-24 Corrigido Erro no Link do Código do ESP32
2026-05-24 Update schematic project link in README
2026-05-26 added breathing LED, changed SCLK to PB13
2026-05-28 Adicionada Documentação dos Sensores
    Adicionadas tabelas e blocos de código na documentação da integração dos sensores
2026-05-28 Concertada Tabela de Novo
2026-05-28 Increase Charge_Temp bit field size to 10 bits
2026-05-28 Update Charge_Temp bit field size in README
2026-05-28 Update sensor data structure and sizes in README
    Altered the bit sizes for the controller temperature and error message fields to allow for individual sensor error reporting.
2026-06-07 PCB layout V1 added - DRC review nedded
    [Modulo_corrente_temperatura_barco_Zenite.kicad_pcb, Modulo_corrente_temperatura_barco_Zenite.kicad_sch]
2026-06-25 Capacitores ajustados
    Corrijido erro DRC
    [Modulo_corrente_temperatura_barco_Zenite.kicad_pcb]
2026-06-26 Updated PCB version - DRC and final routing needed
    [Modulo_corrente_temperatura_barco_Zenite.kicad_pcb, Modulo_corrente_temperatura_barco_Zenite.kicad_sch]
2026-06-28 minor ajustmentes in PCB laytout and schem
    [Modulo_corrente_temperatura_barco_Zenite.kicad_pcb, Modulo_corrente_temperatura_barco_Zenite.kicad_sch]
2026-06-30 Roteamento do AmpOP
    Roteamento do AMpOP na v2.0 da placa - ainda verificando melhorias
    [Modulo_corrente_temperatura_barco_Zenite.kicad_pcb]
2026-06-30 ampop traces modified
    [Modulo_corrente_temperatura_barco_Zenite.kicad_pcb]

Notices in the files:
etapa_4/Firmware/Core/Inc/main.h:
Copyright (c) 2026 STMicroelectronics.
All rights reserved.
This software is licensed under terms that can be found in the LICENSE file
